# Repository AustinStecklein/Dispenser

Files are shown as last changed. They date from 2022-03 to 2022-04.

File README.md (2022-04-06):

# Dispenser
Creedmoor code base for the powder dispenser

# TODO List Software
- [ ] forward and back buttons dont function
- [ ] brightness/sound page sliders need to be prettier if possible
- [ ] calibrate, default settings, power off need yes and no image buttons
- [ ] Force the Subpages of Settings to not appear after clicking on the home button   and then clicking on Settings
- [ ] Keyboard does the same thing as the Settings subpages
- [ ] Replace the Boot Logo when the Program starts with a Creedmoor Logo

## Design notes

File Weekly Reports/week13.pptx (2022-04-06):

## Gantt Chart

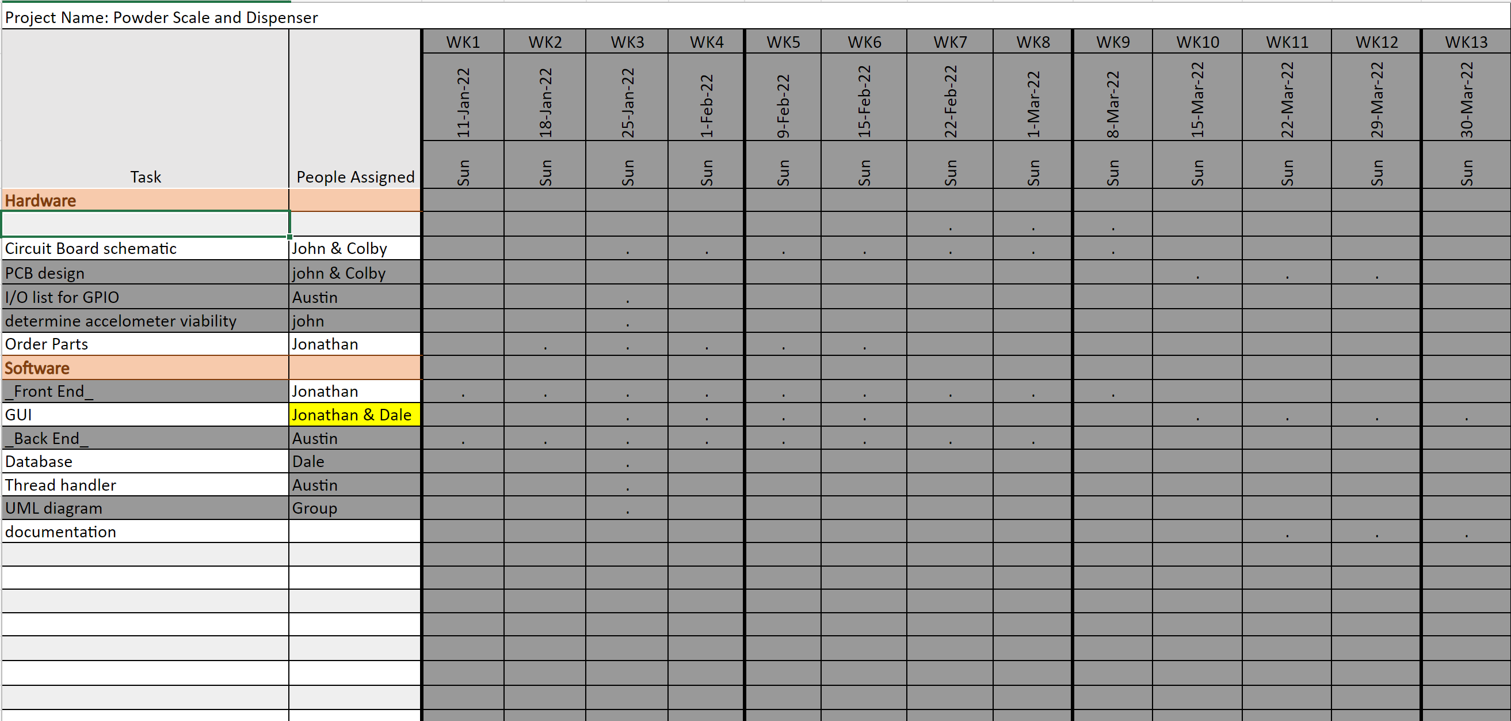
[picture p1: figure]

## Week 13 (30-Mar to 5-Apr) Austin

Goal/Task | % Done | Hours (Act.)

Hours on task during the week (On track ≥ 13 / wk)
Total hours on task so far this semester (On track ≥ 163 hrs)

## Progress made during the week (Log) (What I did)

For example: Resources found (links, manuals), Designs created, Decisions made and corresponding rational, Photos of prototype progress, etc.

## Difficulties encountered during the week (What I did not do and why)

## Goals for this coming week (Ones that move the project forward the most)

Goal/Task | Stop Date (Est.) | Hours (Est.)

Estimated time needed to work on goals for this coming week (typ. 13 hrs)

## How can we help you achieve your goals?

## Week 13 (30-Mar to 5-Apr) Jonathan Phillips

Goal/Task | % Done | Hours (Act.)
Front end - Documentation | N/A | 13
Front end – Fixed <,> buttons | 100 | 2
Front end - Testing | N/A | 3
Presentation | 100 | 0.5

Hours on task during the week (On track ≥ 13 / wk) | 18.5
Total hours on task so far this semester (On track ≥ 163 hrs) | 153

## Progress made during the week (Log) (What I did)

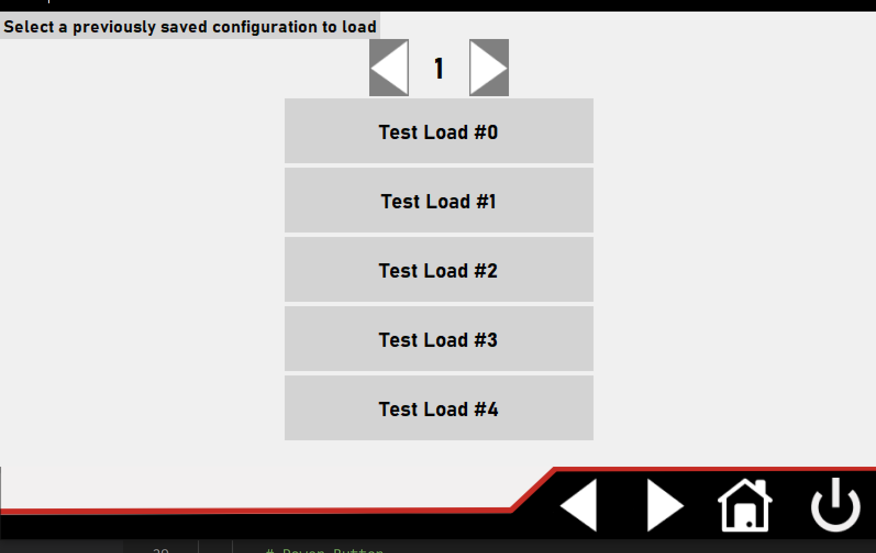
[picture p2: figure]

## Difficulties encountered during the week (What I did not do and why)

- Did not complete everything for Creedmoor due to time constraints

## Goals for this coming week (Ones that move the project forward the most)

Goal/Task | Stop Date (Est.) | Hours (Est.)
N/A | N/A | N/A

Estimated time needed to work on goals for this coming week (typ. 13 hrs) | N/A

## How can we help you achieve your goals?

## Week 13 (30-Mar to 5-Apr) Dale Andreoli

Goal/Task | % Done | Hours (Act.)
Finish comments and documentation | | 5
Final report – software part | | 3
Oral Presentation – create and present | | 4

Hours on task during the week (On track ≥ 13 / wk) | 12
Total hours on task so far this semester (On track ≥ 163 hrs) | 155

## Progress made during the week (Log) (What I did)

Finished comments and documentation
Created slides for presentation
Gave oral presentation with group
Wrote software part of final documentation report

## Difficulties encountered during the week (What I did not do and why)

- Not all backend features were able to be fully implemented such as some of the settings buttons and custom profile features

## Week 13 (30-Mar to 5-Apr) John Stinger

Goal/Task | % Done | Hours (Act.)

Hours on task during the week (On track ≥ 13 / wk)
Total hours on task so far this semester (On track ≥ 163 hrs)

## Progress made during the week (Log) (What I did)

For example: Resources found (links, manuals), Designs created, Decisions made and corresponding rational, Photos of prototype progress, etc.

## Difficulties encountered during the week (What I did not do and why)

## Goals for this coming week (Ones that move the project forward the most)

Goal/Task | Stop Date (Est.) | Hours (Est.)

Estimated time needed to work on goals for this coming week (typ. 13 hrs)

## How can we help you achieve your goals?

## Week 13 (30-Mar to 5-Apr) Colby Hatton

Goal/Task | % Done | Hours (Act.)
Documentation | 100 | 13

Hours on task during the week (On track ≥ 13 / wk)
Total hours on task so far this semester (On track ≥ 163 hrs)

## Progress made during the week (Log) (What I did)

Documented every step of the hardware design for this semesters senior project.

## Difficulties encountered during the week (What I did not do and why)

- Slight confusion in what needs to be done, resulting in some rewriting of parts of the documentation.

## Goals for this coming week (Ones that move the project forward the most)

Goal/Task | Stop Date (Est.) | Hours (Est.)
Graduate! | 4/7 | <5 (Length of the 380 final)

Estimated time needed to work on goals for this coming week (typ. 13 hrs)

## How can we help you achieve your goals?

- Pizza Party?

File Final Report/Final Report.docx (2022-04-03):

Powder Scale and Dispenser

Team A: Dale Andreoli, Colby Hatton, Jonathan Phillips, Austin Stecklein, John Stinger

Index

1. Mission Statement
2. Scope of Work
3. Design Specifications
    i. Stuff
    ii. Things
4. Product Selection
5. Body
  a. Hardware
  b. Software
6. Conclusion

Mission Statement

Design, build, and test the electronics for the dispenser with a touch screen display and controlling two stepper motors by April 6, 2021 with a prototyping budget of $1,000.00 USD and for less than 600 people-hours.

Scope of Work

Design Specifications

Product Selection

- We chose the beaglebone back because that was the board that Creedmoor provided for us and concluded that after the prototype was handed back to Creedmoor they would be able to move the project along faster versus using a different board. We also choose to use the GeeekPi screen due to the high volumes of stock available at Digikey, and other website, when it came time for Creedmoor to mass produce.

Body

User’s Manual

- The primary function of the prototype is to dispense powder according to a user inputted value which then displays the current value on the scale to the prototype’s user interface.
- The prototype consists of beaglebone black wireless development board, with a powder scale connected to it via an USB connection, as well as an user interface displayed on a 5 inch screen, which is the way by which the user interacts with the prototype.

Developer’s Report

Software

- The programming language used to create the front and back end of the user interface was Python. We chose Python because it is a relatively easy language to learn, read, and understand.
- As previously mentioned, the software is broken up into 2 major sections: the front end and the back end. The front end is then broken up into different pages, each with their own purpose and function. The home page is the first screen users will see after booting up the prototype. However, the home page, and every other page, is slightly covered by another page known as main. Main consists of a black bar with 4 buttons, which allow the user to navigate directly back to the home page and turn off the prototype. The settings page is a hub for the different types of settings an user could interact with, for example, the brightness and sound of the prototype. When the user wants to create a new profile, or Load Card, they can click on the Save button on the home page and are directed to a page containing a filename along with several other fields that are involved with reloading ammunition. The user can save their own values and make notes onto a Load Card, and store that information for future use, which allows them to switch between Load Card depending on their current needs.
- The back end…
- The front end is designed to run on every machine, however, the back end is designed to run on a beaglebone black board with the powder scale feeding the beaglebone information via an USB connection.

Conclusion

The dispenser

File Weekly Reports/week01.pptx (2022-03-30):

## Creedmoor Powder Dispenser

## Weekly progress (Hardware)

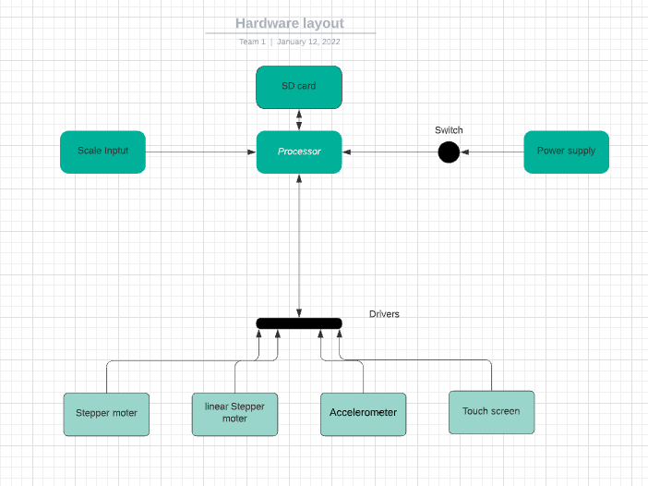
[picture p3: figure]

## Weekly progress (software)

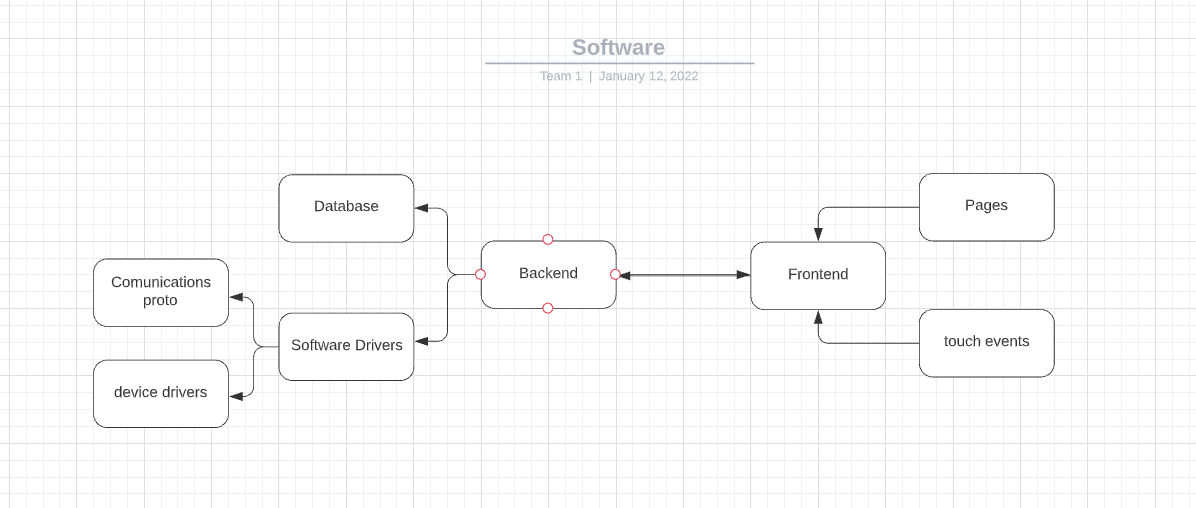
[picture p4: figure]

## Week 1 (5-Jan to 11-Jan) Austin Stecklein

Goal/Task | % Done | Hours (Act.)
Everyone Complete Leadership Foundation: Clarify Purpose (p. 32-33), Team Purpose Statement (p. 34), Voice Finder (p. 64-67), Your Contribution Statement (p. 68), Win-Win Performance Agreement (p. 76) | 0 | 0
Team Complete: Project Objective / Mission Statement (clear and concise, <25 words, see example below) | 100 | .5
Team Complete: Project Task Template (A Gantt Chart) (Conditions or tasks that must be completed, work that needs to be done) | 0 | 0
Flow charts for hardware and software | 100 | 5.5

Example Project Objective / Mission Statements
Power Scale Dispenser:
Design, build, and test the electronics for the dispenser with a touch screen display and controlling two stepper motors by April 6, 2021 with a prototyping budget of $XXX USD and for less than 600 people-hours.
For ideas, also read Mission Questions in I-Learn | Content | Resources | Mission Questions

Hours on task during the week (On track ≥ 13 / wk) | 6
Total hours on task so far this semester (On track ≥ 13 hrs) | 13

## Progress made during the week (Log) (What I did)

- Created general software and hardware layout
- Researched hardware parts

## Difficulties encountered during the week (What I did not do and why)

- Defining scope of project

## Goals for this coming week (Ones that move the project forward the most)

Goal/Task | Stop Date (Est.) | Hours (Est.)
Selecting processor for project with rest of the group. | 1/14/21 | 1
Researching drivers for stepper motors | 1/16/21 | 2
developing backend framework with chosen programming language | 1/26/21 | 10

Estimated time needed to work on goals for this coming week (typ. 13 hrs) | 13

## How can we help you achieve your goals?

- Understanding more of the final product

## Week 1 (5-Jan to 11-Jan) Jonathan Phillips

Goal/Task | % Done | Hours (Act.)
Everyone Complete Leadership Foundation: Clarify Purpose (p. 32-33), Team Purpose Statement (p. 34), Voice Finder (p. 64-67), Your Contribution Statement (p. 68), Win-Win Performance Agreement (p. 76)
Team Complete: Project Objective / Mission Statement (clear and concise, <25 words, see example below)
Team Complete: Project Task Template (A Gantt Chart) (Conditions or tasks that must be completed, work that needs to be done)

Power Scale Dispenser:
Design, build, and test the electronics for the dispenser with a touch screen display and controlling two stepper motors by April 6, 2021 with a prototyping budget of $XXX USD and for less than 600 people-hours.

Hours on task during the week (On track ≥ 13 / wk)
Total hours on task so far this semester (On track ≥ 13 hrs)

## Progress made during the week (Log) (What I did)

- Created a Gannt Chart for the layout for the hardware and software
- Researched different LCDs that could be used for the touch screen display

## Difficulties encountered during the week (What I did not do and why)

- Did not order the LCD screen yet due to it needing to be approved first by the group

## Goals for this coming week (Ones that move the project forward the most)

Goal/Task | Stop Date (Est.) | Hours (Est.)
Finalize parts for the project and order them | 1/13/22 | 1
Start Development on the Front End framework | 1/26/22 | 12

Estimated time needed to work on goals for this coming week (typ. 13 hrs) | 13

## How can we help you achieve your goals?

- Do you have a preference on what the screen will be?

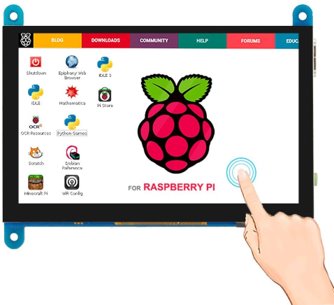
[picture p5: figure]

Elecrow

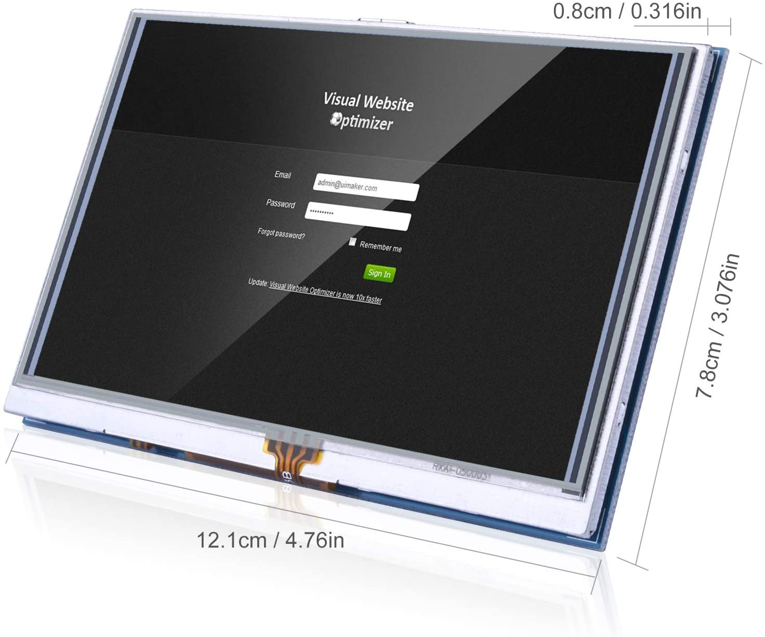
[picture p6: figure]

Kuman

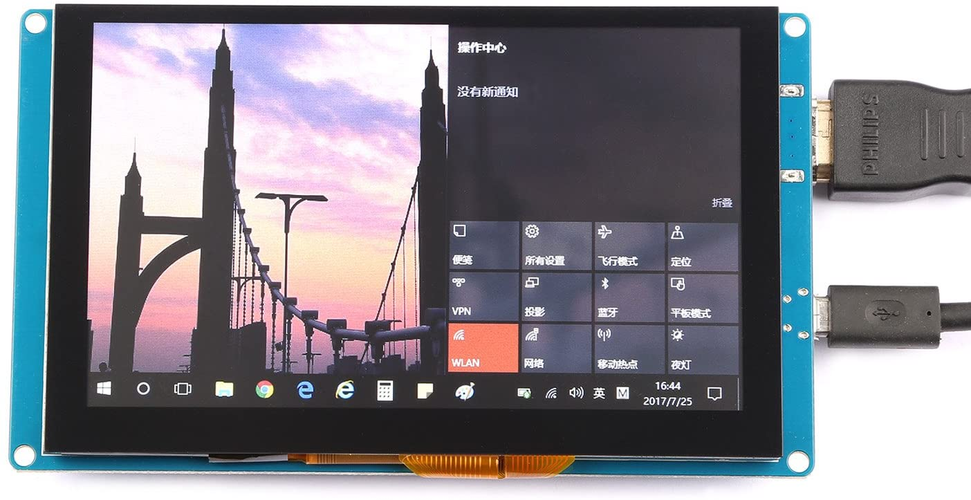
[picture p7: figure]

GeeekPi

## Week 1 (5-Jan to 11-Jan) Dale Andreoli

Goal/Task | % Done | Hours (Act.)
Everyone Complete Leadership Foundation: Clarify Purpose (p. 32-33), Team Purpose Statement (p. 34), Voice Finder (p. 64-67), Your Contribution Statement (p. 68), Win-Win Performance Agreement (p. 76) | 0 | 0
Team Complete: Project Objective / Mission Statement (clear and concise, <25 words, see example below) | 100 | 1
Team Complete: Project Task Template (A Gantt Chart) (Conditions or tasks that must be completed, work that needs to be done) | 35 | 1

Example Project Objective / Mission Statements
Power Scale Dispenser:
Design, build, and test the electronics for the dispenser with a touch screen display and controlling two stepper motors by April 6, 2021 with a prototyping budget of $XXX USD and for less than 600 people-hours.
For ideas, also read Mission Questions in I-Learn | Content | Resources | Mission Questions

Hours on task during the week (On track ≥ 13 / wk) | 5
Total hours on task so far this semester (On track ≥ 13 hrs) | 5

## Progress made during the week (Log) (What I did)

- Researched potential processors

## Difficulties encountered during the week (What I did not do and why)

- Determining what we need to do and how to divide it

## Goals for this coming week (Ones that move the project forward the most)

Goal/Task | Stop Date (Est.) | Hours (Est.)
Research potential processors | 1/14/21 | 2
Collaborate as a group to determine which processors would be best | 1/16/21 | 4
Research methods to implement necessary drivers | 1/26/21 | 6

Estimated time needed to work on goals for this coming week (typ. 13 hrs) | 12

## How can we help you achieve your goals?

- Clarify/Answer Questions

## Week 1 (5-Jan to 11-Jan) Colby Hatton

Goal/Task | % Done | Hours (Act.)
Everyone Complete Leadership Foundation: Clarify Purpose (p. 32-33), Team Purpose Statement (p. 34), Voice Finder (p. 64-67), Your Contribution Statement (p. 68), Win-Win Performance Agreement (p. 76)
Team Complete: Project Objective / Mission Statement (clear and concise, <25 words, see example below)
Team Complete: Project Task Template (A Gantt Chart) (Conditions or tasks that must be completed, work that needs to be done)

Project Objective / Mission Statements
Power Scale Dispenser:
Design, build, and test the electronics for the dispenser with a touch screen display and controlling two stepper motors by April 6, 2021 with a prototyping budget of $XXX USD and for less than 600 people-hours.
For ideas, also read Mission Questions in I-Learn | Content | Resources | Mission Questions

Hours on task during the week (On track ≥ 13 / wk) | ~5
Total hours on task so far this semester (On track ≥ 13 hrs) | ~5

## Progress made during the week (Log) (What I did)

- Helped create general software and hardware layout
- Purchased leadership book
- Preliminary research

## Difficulties encountered during the week (What I did not do and why)

- No problems yet

## Goals for this coming week (Ones that move the project forward the most)

Goal/Task | Stop Date (Est.) | Hours (Est.)
Find, compare, and form opinions on the correct processor for our project. | 1/14/22 | 4
Selecting processor for project with rest of the group. | 1/16/22 | 1
Obtain, test, and experiment with given hardware | 1/16/22 | 3
Class time, presentations, workbook, etc. | 1/16/22 | 4

Estimated time needed to work on goals for this coming week (typ. 13 hrs) | 13

## How can we help you achieve your goals?

- Communication - Ensure lines work and communication is clear.

## Week 1 (5-Jan to 11-Jan) John Stinger

Goal/Task | % Done | Hours (Act.)
Everyone Complete Leadership Foundation: Clarify Purpose (p. 32-33), Team Purpose Statement (p. 34), Voice Finder (p. 64-67), Your Contribution Statement (p. 68), Win-Win Performance Agreement (p. 76)
Team Complete: Project Objective / Mission Statement (clear and concise, <25 words, see example below)
Team Complete: Project Task Template (A Gantt Chart) (Conditions or tasks that must be completed, work that needs to be done)

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

Hours on task during the week (On track ≥ 13 / wk) | 12
Total hours on task so far this semester (On track ≥ 13 hrs) | 12

## Progress made during the week (Log) (What I did)

Researched different processors and possible boards to use in the project.

Atmel ARM based microprocessor would be best.

Raspberry Pi Zero 2 would be effective and affordable, but generally unavailable.

Do we want a commercially available board?

## Difficulties encountered during the week (What I did not do and why)

- Select a specific processor. Needed to meet with the team to discuss options.

## Goals for this coming week (Ones that move the project forward the most)

Goal/Task | Stop Date (Est.) | Hours (Est.)
Select a Processor | | 1
Define the exact scope of the project | | 2
Define individual roles | | 1
Purchasing a Board | | 2

Estimated time needed to work on goals for this coming week (typ. 13 hrs)

## How can we help you achieve your goals?

- More than one day to do research and meet with the team.

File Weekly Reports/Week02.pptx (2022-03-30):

## Week 2 (13-Jan to 18-Jan)

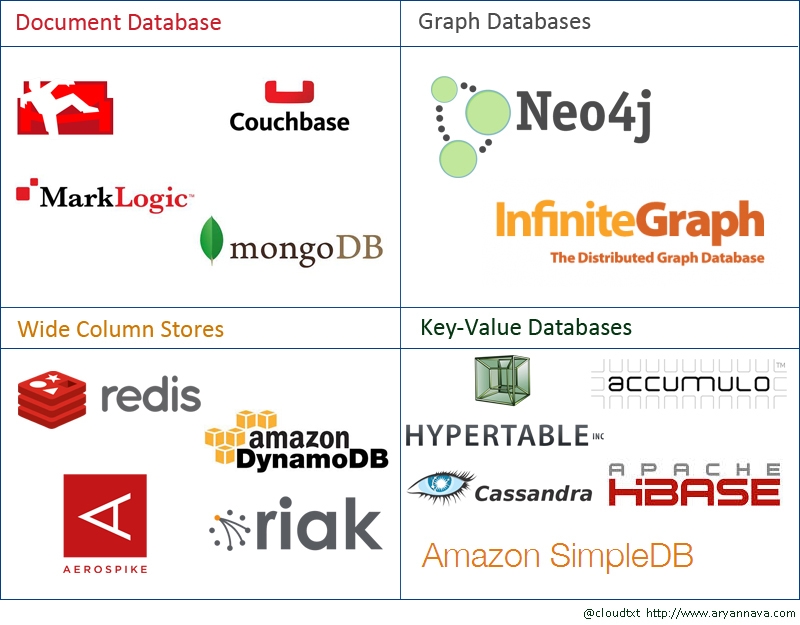
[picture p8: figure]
NoSQL vs SQL | What is Difference between SQL and NoSQL |
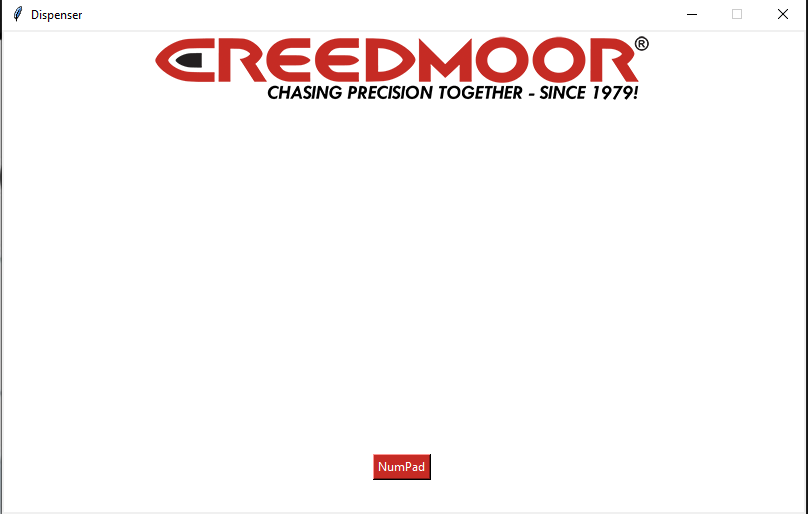
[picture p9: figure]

## Week 2 (13-Jan to 18-Jan) Austin Stecklein

Goal/Task | % Done | Hours (Act.)
Backend (event handling and threading) | 50 | 8
I/O list for circuit schematic | 100 | 1
Drivers for steppers and accleometer | 10 | 4

Hours on task during the week (On track ≥ (13) / wk) | 13
Total hours on task so far this semester (On track ≥ 26 hrs) | 26

## Progress made during the week (Log) (What I did)

Created event handler and successfully test running events from a pop GUI
Create I/O list for use in schematic
MicroSD card on order

## Difficulties encountered during the week (What I did not do and why)

- No SD card was found in package

## Goals for this coming week (Ones that move the project forward the most)

Goal/Task | Stop Date (Est.) | Hours (Est.)
Finish event handler by allowing data to pass from the thread back to the GUI | 1/26 | 6
Get Code onto the beagle board | 1/26 | 2
Get stepper motor driver working | 1/26 | 6

Estimated time needed to work on goals for this coming week (typ. 13 hrs) | 14

## How can we help you achieve your goals?

## Week 2 (12-Jan to 18-Jan) Dale Andreoli

Goal/Task | % Done | Hours (Act.)
Everyone Complete Leadership Foundation: Clarify Purpose (p. 32-33), Team Purpose Statement (p. 34), Voice Finder (p. 64-67), Your Contribution Statement (p. 68), Win-Win Performance Agreement (p. 76) | 0 | 0
Research database options – Amazon Dynamo DB | 100 | 3
Assist with GUI – Research tkinter Python library, create mockup | 10 | 1

Project Objective / Mission Statements
Power Scale Dispenser:
Design, build, and test the electronics for the dispenser with a touch screen display and controlling two stepper motors by April 6, 2021 with a prototyping budget of $XXX USD and for less than 600 people-hours.

Hours on task during the week | 4
Total hours on task so far this semester | 17

## Progress made during the week (Log) (What I did)

- Collaborated with Austin on our needs for backend software
- Researched NoSQL database options
  - Amazon Dynamo DB should fit our needs

## Difficulties encountered during the week (What I did not do and why)

- No problems yet

## Goals for this coming week (Ones that move the project forward the most)

Goal/Task | Stop Date (Est.) | Hours (Est.)
Work with Jonathon to design GUI | 1/23/21 | 3
Implement GUI features | 1/24/21 | 6
Collaborate with Austin to determine what drivers will need to be written | 1/23/21 | 2

Estimated time needed to work on goals for this coming week | 11

## How can we help you achieve your goals?

- GUI thoughts and ideas

## Week 2 (13-Jan to 18-Jan) John Stinger

Goal/Task | % Done | Hours (Act.)
Decide on a specific development board for the project. | 100% | 3
Meet with team to discus the scope and define roles | 100% | 2

Hours on task during the week (On track ≥ (13) / wk) | 10
Total hours on task so far this semester (On track ≥ 26 hrs) | 22

## Progress made during the week (Log) (What I did)

For example: Resources found (links, manuals), Designs created, Decisions made and corresponding rational, Photos of prototype progress, etc.

- Inspected the material received

- Decided to continue using the provided Beagle Board for development

- Defined the scope better and the individual roles and goals

## Difficulties encountered during the week (What I did not do and why)

- None

## Goals for this coming week (Ones that move the project forward the most)

Goal/Task | Stop Date (Est.) | Hours (Est.)
Check viability of current accelerometer | | 2
Start the drafting of the circuit board | | 10 +

Estimated time needed to work on goals for this coming week (typ. 13 hrs) | 12 +

## How can we help you achieve your goals?

- Continued direction

- Advice on circuit building software

- Did we want any kind of wireless capabilitie?

- Can the power supply be its own board?

## Week 2 (13-Jan to 18-Jan) Jonathan Phillips

Goal/Task | % Done | Hours (Act.)
Reviewed the Hardware sent from Creedmoor | 100 | 1.5
Ordered the LCD Screen (Arriving Today) | 100 | 0.5
Worked on the front end | TBD | 5

Hours on task during the week (On track ≥ (13) / wk)
Total hours on task so far this semester (On track ≥ 26 hrs)

## Progress made during the week (Log) (What I did)

For example: Resources found (links, manuals), Designs created, Decisions made and corresponding rational, Photos of prototype progress, etc.

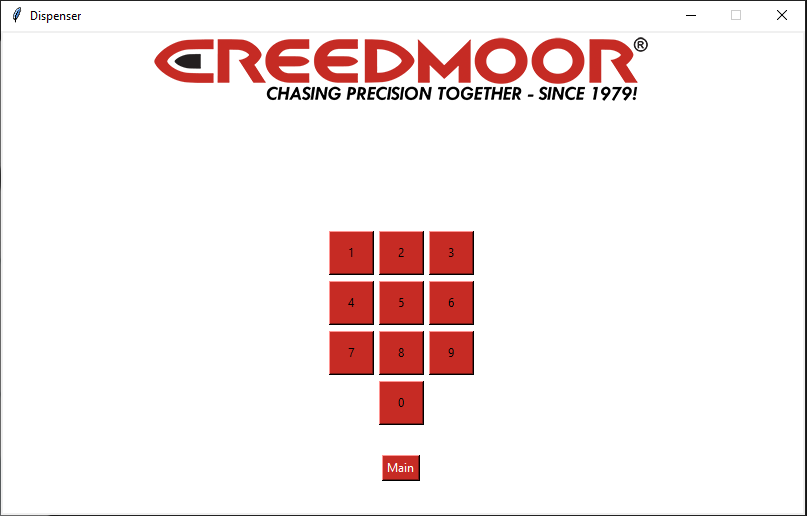
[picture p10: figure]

## Difficulties encountered during the week (What I did not do and why)

- Understanding Python

## Goals for this coming week (Ones that move the project forward the most)

Goal/Task | Stop Date (Est.) | Hours (Est.)
UML Diagram for the frontend | 1/25/22 | 1.5
Continue working on the frontend | Ongoing | 11.5

Estimated time needed to work on goals for this coming week (typ. 13 hrs) | 13

## How can we help you achieve your goals?

- Do you have an idea of what you would like the layout of the display to be?

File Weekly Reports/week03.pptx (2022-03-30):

## Week 3 (19-Jan to 25-Jan)

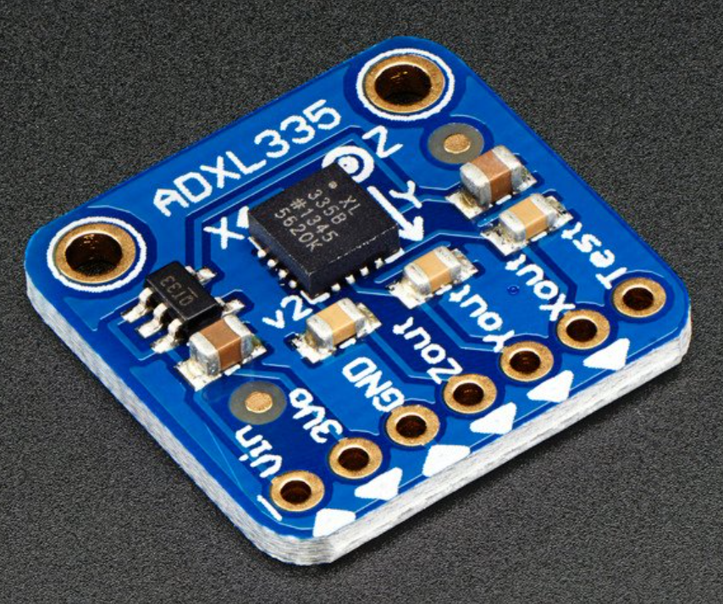
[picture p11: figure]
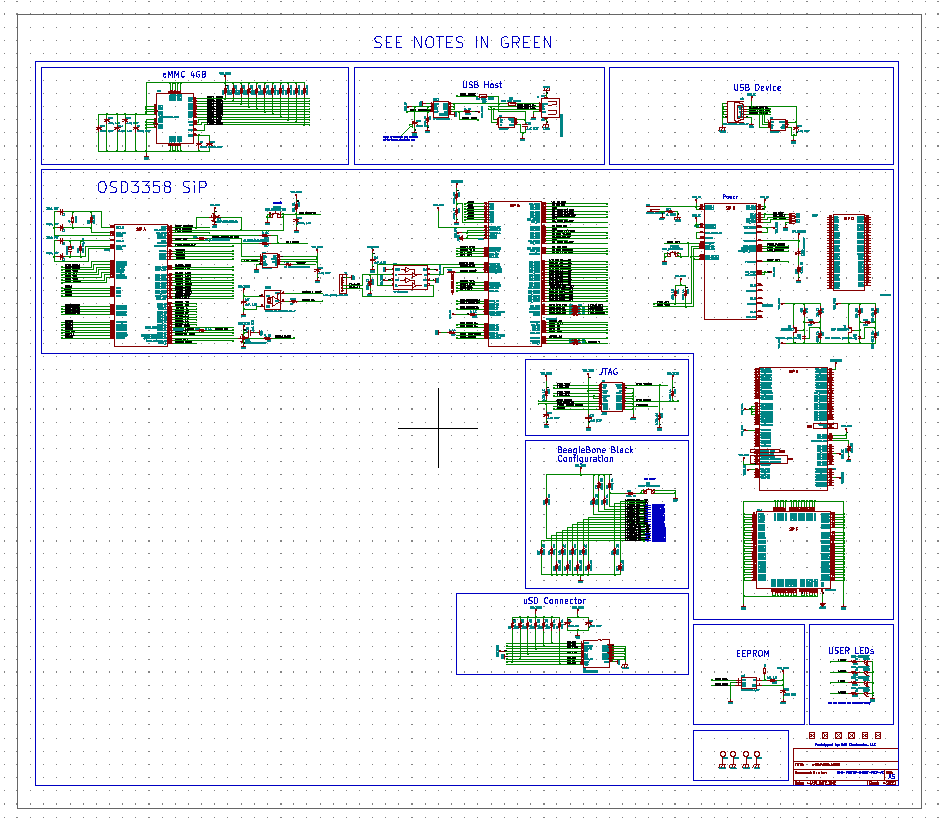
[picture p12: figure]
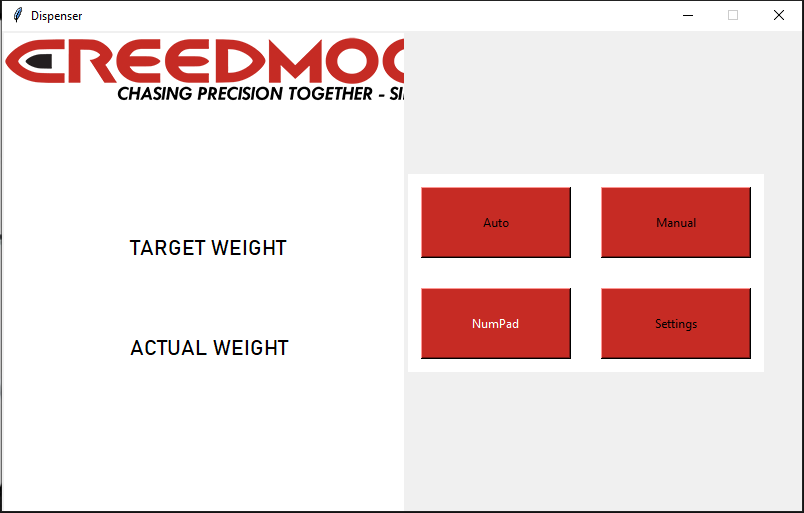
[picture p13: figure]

## Week 3 (19-Jan to 25-Jan) Austin Stecklein

Goal/Task | % Done | Hours (Act.)
Get stepper motor driver working | 80 | 6
Get Code onto the beagle board | 100 | 2
Finish event handler by allowing data to pass from the thread back to the GUI | 100 | 4

Hours on task during the week (On track ≥ (10) / wk) | 12
Total hours on task so far this semester (On track ≥ 36 hrs) | 30

## Progress made during the week (Log) (What I did)

Re-flashed memory on the Beaglebone black
Used PWM library to control the stepper motors more accurately
Uploaded code onto the Beaglebone black
Finished backend event framework

## Difficulties encountered during the week (What I did not do and why)

- Flashing the Board had some hiccups
- Understanding the usb capabilities

## Goals for this coming week (Ones that move the project forward the most)

Goal/Task | Stop Date (Est.) | Hours (Est.)
Finish stepper motor drivers | 2/2/2022 | 2
Get database framework | 2/2/2022 | 3
Start interfacing with prototype GUI | 2/2/2022 | 6

Estimated time needed to work on goals for this coming week (typ. 13 hrs) | 11

## Week 3 (19-Jan to 25-Jan) Colby Hatton

Goal/Task | % Done | Hours (Act.)
Determine Which CAD Software to Use | 90 | 3
Create Basic Schematic and Accustom self to CAD Software | 60 | 5
Find Component Symbols/Footprints | 40 | 5

Hours on task during the week (On track ≥ (10) / wk) | 13
Total hours on task so far this semester (On track ≥ 36 hrs) | ~35

## Progress made during the week (Log) (What I did)

Determined that we will be using KiCad to design and lay out our project.
Found Footprint and Symbol Libraries for several components we will be using.
Successfully found and Imported the Beagle Board Black Wireless board and Schematic

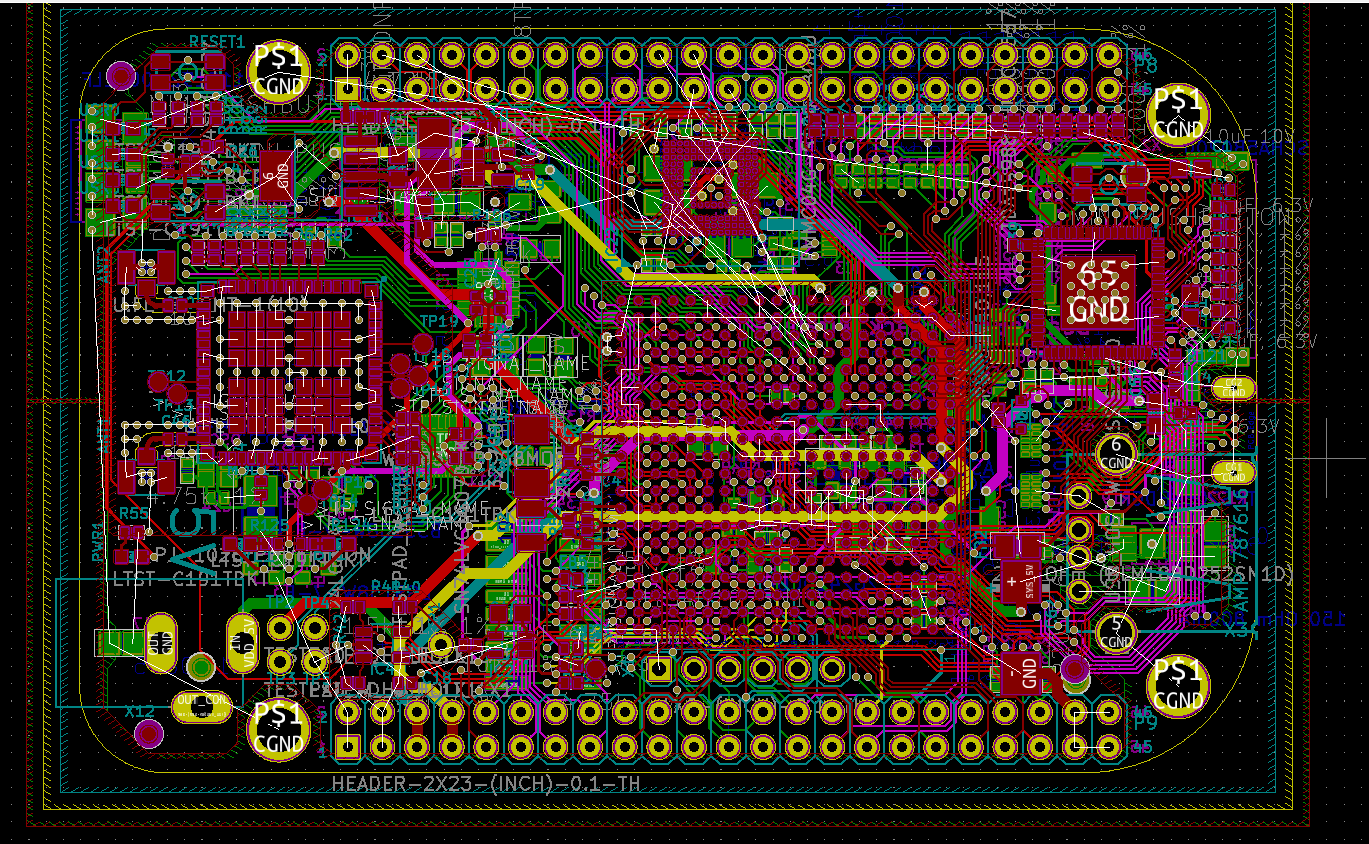
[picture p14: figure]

## Difficulties encountered during the week (What I did not do and why)

- Certain components out of production
- Need to find alternate and ensure they are compatible with the same pinout

## Goals for this coming week (Ones that move the project forward the most)

Goal/Task | Stop Date (Est.) | Hours (Est.)
Acquire footprints/symbols for the components we will be using | 2/9 | 6
Finish/Wire schematic for our PCB | 2/16 | 20
(Possibly) Plan layout of the board | 2/16 | 5

Estimated time needed to work on goals for this coming week (typ. 13 hrs) | ~15

## Week 3 (19-Jan to 25-Jan) Dale Andreoli

Goal/Task | % Done | Hours (Act.)
Assist with GUI design/mockup | 90 | 3
GUI – Number pad module | 85 | 8

Project Objective / Mission Statements
Power Scale Dispenser:
Design, build, and test the electronics for the dispenser with a touch screen display and controlling two stepper motors by April 6, 2021 with a prototyping budget of $XXX USD and for less than 600 people-hours.

Hours on task during the week | 11
Total hours on task so far this semester | 30

## Progress made during the week (Log) (What I did)

Collaborated with Jonathon on the GUI
Created a Number Pad module that can be easily added into the GUI

## Goals for this coming week (Ones that move the project forward the most)

Goal/Task | Stop Date (Est.) | Hours (Est.)
Next GUI module: Pop out menu | 2/1/21 | 8
Collaborate with Jonathan for GUI needs | 2/1/21 | 3

Estimated time needed to work on goals for this coming week | 11

## How can we help you achieve your goals?

- Jonathan and I will reach out to Christian, Kelby and Wayne for GUI feedback.

## Week 3 (19-Jan to 25-Jan) John Stinger

Goal/Task | % Done | Hours (Act.)
Check viability of current accelerometer | 100% | 2
Start the drafting of the circuit board | 100% | 4

Hours on task during the week (On track ≥ (10) / wk) | 6
Total hours on task so far this semester (On track ≥ 36 hrs)

## Progress made during the week (Log) (What I did)

For example: Resources found (links, manuals), Designs created, Decisions made and corresponding rational, Photos of prototype progress, etc.

- 3 axis will be fine
- Both the premade card and buying the chip would be viable
- Started the modeling with Colby on KiCad

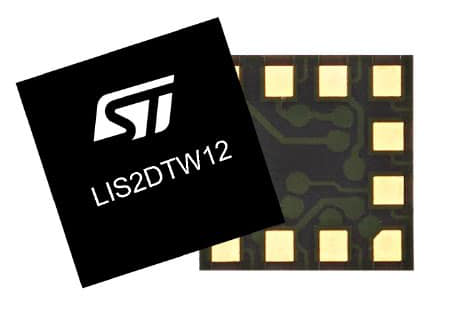
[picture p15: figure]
LIS2DTW12TR

## Difficulties encountered during the week (What I did not do and why)

- none

## Goals for this coming week (Ones that move the project forward the most)

Goal/Task | Stop Date (Est.) | Hours (Est.)
Continue to model the circuit card on the computer. | | 10+
Learn how to make the motor drivers more robust. | | 3

Estimated time needed to work on goals for this coming week (typ. 13 hrs)

## How can we help you achieve your goals?

- Continue to be available for reference.

## Week 3 (19-Jan to 25-Jan) Jonathan Phillips

Goal/Task | % Done | Hours (Act.)
UML Mockup | 100 | 1
Front End | N/A | 6.5

Hours on task during the week (On track ≥ (10) / wk) | 8.5
Total hours on task so far this semester (On track ≥ 36 hrs)

## Progress made during the week (Log) (What I did)

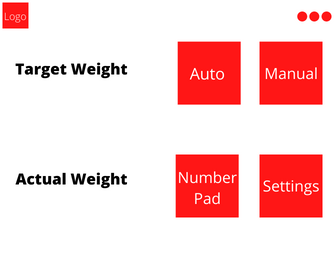
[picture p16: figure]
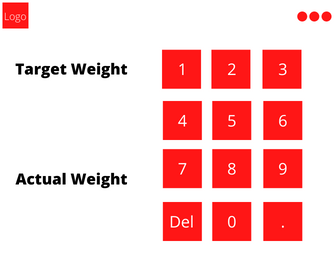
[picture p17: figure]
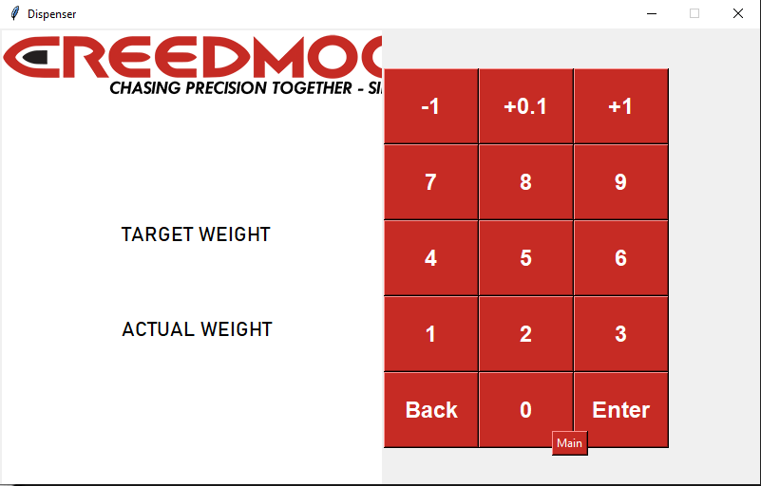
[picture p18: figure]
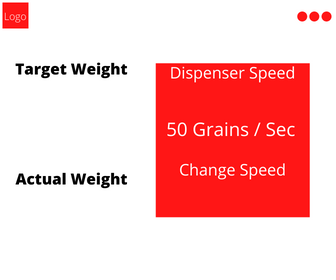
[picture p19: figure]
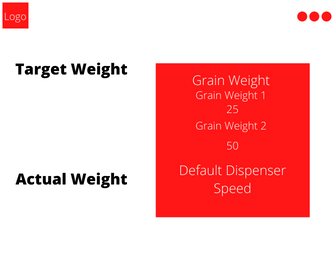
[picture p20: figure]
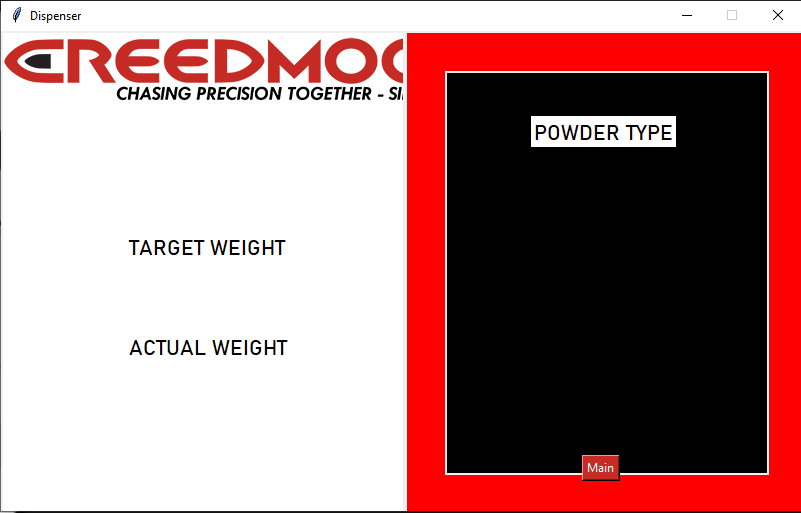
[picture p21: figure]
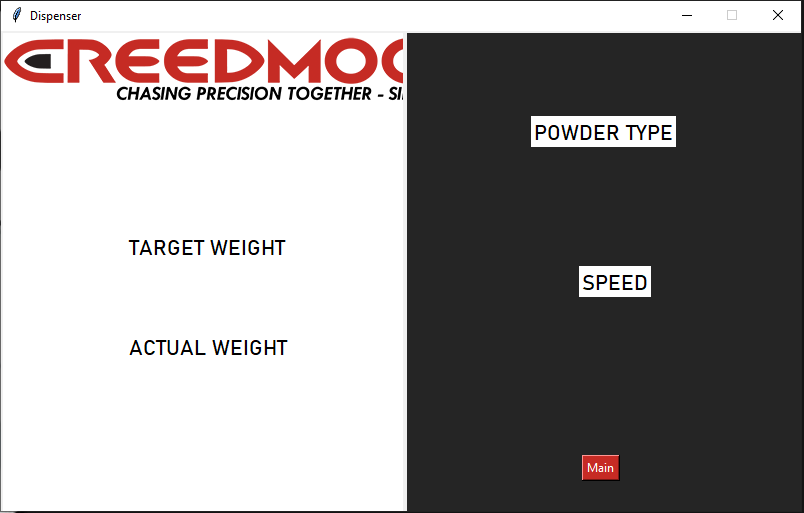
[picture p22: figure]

Front end

UML Mockup

## Difficulties encountered during the week (What I did not do and why)

- Learning Python syntax

## Goals for this coming week (Ones that move the project forward the most)

Goal/Task | Stop Date (Est.) | Hours (Est.)
Front end | Ongoing | 13

Estimated time needed to work on goals for this coming week (typ. 13 hrs) | 13

## How can we help you achieve your goals?

- Any comments on the mockup or overall design of the front end?

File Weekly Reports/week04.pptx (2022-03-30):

## Week 4 (26-Jan to 1-Feb) Austin Stecklein

Goal/Task | % Done | Hours (Act.)
Finish stepper motor drivers | 100 | 4
Get database framework | 50 | 3
Investigate hardware | 50 | 6

Hours on task during the week (On track ≥ 13 / wk) | 13
Total hours on task so far this semester (On track ≥ 49 hrs) | 43

## Progress made during the week (Log) (What I did)

Software stepper drivers are complete
Database framework is moving along
Ordered another beagle bone to replace broken hardware

## Difficulties encountered during the week (What I did not do and why)

- Blowing up the hardware

## Goals for this coming week (Ones that move the project forward the most)

Goal/Task | Stop Date (Est.) | Hours (Est.)
Finish investigating hardware | 2/10/2021 | 4
Finish database | 2/10/2021 | 4
Help with GUI | 2/10/2021 | 6

Estimated time needed to work on goals for this coming week (typ. 13 hrs) | 14

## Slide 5

Week 4 (26-Jan to 1-Feb) Colby Hatton

Goal/Task | % Done | Hours (Act.)
Finish Schematic | 70 | 6
Finish PCB | 5 | 1
Part/Research

Hours on task during the week (On track ≥ 13 / wk)
Total hours on task so far this semester (On track ≥ 49 hrs)

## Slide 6

Progress made during the week (Log)
(What I did)

Found and applied parts to Schematic (Mostly connectors)
Researched Memory Module
Attempted to fix BeagleBoard

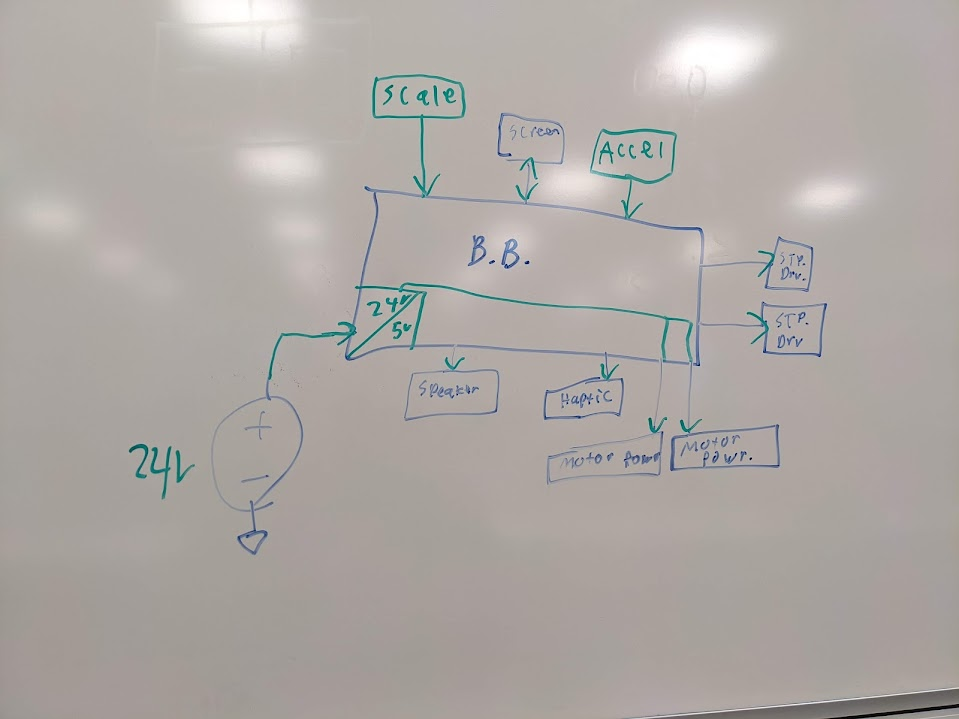
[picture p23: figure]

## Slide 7

Difficulties encountered during the week
(What I did not do and why)

- Assign lines to pins
- Physical Work with the BeagleBoard

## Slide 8

Goals for this coming week
(Ones that move the project forward the most)

Goal/Task | Stop Date (Est.) | Hours (Est.)
Finish Schematic | | 4
Begin Layout | | 8

Estimated time needed to work on goals for this coming week (typ. 13 hrs)

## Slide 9

How can we help you achieve your goals?

- Part Acquisition
- Line Assignments

## Week 4 (26-Jan to 2-Feb) Dale Andreoli

Goal/Task | % Done | Hours (Act.)
Collaborate with team on UI design and implementation | 100 | 2
Research open source projects to save time creating GUI modules from scratch | 50 | 3
Research other potential libraries to use instead of tkinter | 50 | 1
Implement GUI modules | 15 | 6

Project Objective / Mission Statements
Power Scale Dispenser:
Design, build, and test the electronics for the dispenser with a touch screen display and controlling two stepper motors by April 6, 2021 with a prototyping budget of $1000 USD and for less than 600 people-hours.

Hours on task during the week | 12
Total hours on task so far this semester | 42

## Progress made during the week (Log) (What I did)

Collaborated with team on UI design and implementation
Researched libraries and projects to save time creating GUI modules from scratch
Researched other potential libraries to use instead of tkinter

## Difficulties encountered during the week (What I did not do and why)

- We now have a nice clear plan for what the UI needs

## Goals for this coming week (Ones that move the project forward the most)

Goal/Task | Stop Date (Est.) | Hours (Est.)
Find or design a touch keyboard module to be used in the GUI | Feb 9th | 9
Collaborate with Jonathan and Austin on GUI implementation | | 3

Estimated time needed to work on goals for this coming week | 12

## Week 4 (26-Jan to 1-Feb) John Stinger

Goal/Task | % Done | Hours (Act.)
Board Design | 15% | 4
Component Selection | 70% | 4
Team Meetings and Discussions | | 3

Hours on task during the week (On track ≥ 13 / wk) | 11
Total hours on task so far this semester (On track ≥ 49 hrs) | 39

## Progress made during the week (Log) (What I did)

For example: Resources found (links, manuals), Designs created, Decisions made and corresponding rational, Photos of prototype progress, etc.

- Continued the board design process
- Selected components for the I/O connections
- Ordered the components

## Difficulties encountered during the week (What I did not do and why)

- Certain components were unorderable

## Goals for this coming week (Ones that move the project forward the most)

Goal/Task | Stop Date (Est.) | Hours (Est.)
Continue to work on the board schematic | | 6
Continue to work on the board layout | | 6

Estimated time needed to work on goals for this coming week (typ. 13 hrs) | 12

## How can we help you achieve your goals?

- Is the motor drivers going to be integrated into the main board?

## Week 4 (26-Jan to 1-Feb) Jonathan Phillips

Goal/Task | % Done | Hours (Act.)
Front End | N/A | 11

Hours on task during the week (On track ≥ 13 / wk) | 11
Total hours on task so far this semester (On track ≥ 49 hrs) | 40

## Progress made during the week (Log) (What I did)

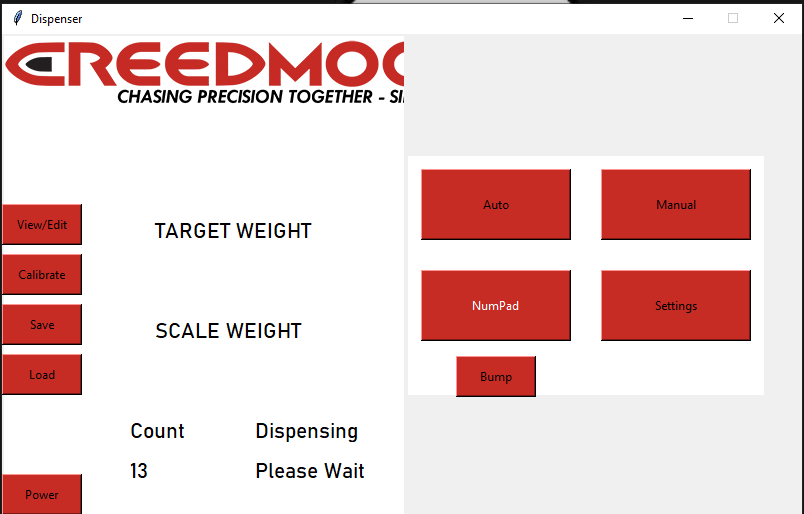
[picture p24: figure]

## Difficulties encountered during the week (What I did not do and why)

- The buttons cannot be modified that much using this python library,
However, the buttons can be made using images instead

## Goals for this coming week (Ones that move the project forward the most)

Goal/Task | Stop Date (Est.) | Hours (Est.)
Front End | 4/1/22 | 13

Estimated time needed to work on goals for this coming week (typ. 13 hrs) | 13

## How can we help you achieve your goals?

- Refining UI Design and Layout

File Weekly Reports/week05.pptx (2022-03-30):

## Week 5 (2-Feb to 8-Feb)


## Week 5 (2-Feb to 8-Feb) Austin Stecklein

Goal/Task | % Done | Hours (Act.)
Investigating hardware | 100 | 3
Finish database | 99 | 4
Backend events | 75 | 6

Hours on task during the week (On track ≥ 13 / wk) | 13
Total hours on task so far this semester (On track ≥ 62 hrs) | 56

## Progress made during the week (Log) (What I did)

Found that voltage regular to be the problem. Will take these lessons learned for future hardware
Finish database and interface for the GUI.
Continued to work on the PID and physical events.

## Difficulties encountered during the week (What I did not do and why)

- None

## Goals for this coming week (Ones that move the project forward the most)

Goal/Task | Stop Date (Est.) | Hours (Est.)
Finish backend events and start testing them with replacement beagle bone (lower voltage this time) | 2/16/2021 | 6
Finish PID and start experimenting with finding the best coefficients | 2/16/2021 | 5
Start merging GUI and backend | 2/16/2021 | 4

Estimated time needed to work on goals for this coming week (typ. 13 hrs) | 15

## Week 5 (2-Feb to 8-Feb) John Stinger

Goal/Task | % Done | Hours (Act.)
Continue to work on the board schematic | | 4
Continue to work on the board layout | | 4
Other | | 4

Hours on task during the week (On track ≥ 13 / wk) | 12
Total hours on task so far this semester (On track ≥ 62 hrs) | 51

## Progress made during the week (Log) (What I did)

- Board development
- Found different connectors
- Started testing speakers

## Difficulties encountered during the week (What I did not do and why)

- none

## Goals for this coming week (Ones that move the project forward the most)

Goal/Task | Stop Date (Est.) | Hours (Est.)
Continued Development of the board | Ongoing | 7
Research how to design better board drivers | | 3

Estimated time needed to work on goals for this coming week (typ. 13 hrs) | 12

## How can we help you achieve your goals?

- Continued Support

## Week 5 (2-Feb to 8-Feb) Colby Hatton

Goal/Task | % Done | Hours (Act.)
Schematic Work | 85% | 10
Layout | 5% | 1
Parts/Resarch/Testing | 80% | 2

Hours on task during the week (On track ≥ 13 / wk)
Total hours on task so far this semester (On track ≥ 62 hrs) | 51

## Progress made during the week (Log) (What I did)

Preformed MicroSD boot, verified speaker arrangement, prepared pin layout

## Difficulties encountered during the week (What I did not do and why)

- Finding a good motor driver

## Goals for this coming week (Ones that move the project forward the most)

Goal/Task | Stop Date (Est.) | Hours (Est.)
Obtain Motor Driver | Ongoing | 13
Finish Schematic
Contuine Layout

Estimated time needed to work on goals for this coming week (typ. 13 hrs) | 13

## How can we help you achieve your goals?

- Continued Support, consistently updated line/signal list

## Week 5 (3-Feb to 9-Feb) Dale Andreoli

Goal/Task | % Done | Hours (Act.)
Find or create a touch keyboard module to slot into the GUI | 80% | 5
Collaborate with Jonathan and Austin on GUI implementation | | 9

Project Objective / Mission Statements
Power Scale Dispenser:
Design, build, and test the electronics for the dispenser with a touch screen display and controlling two stepper motors by April 6, 2021 with a prototyping budget of $1000 USD and for less than 600 people-hours.

Hours on task during the week | 14
Total hours on task so far this semester | 56

## Progress made during the week (Log) (What I did)

Found a keyboard that should suit our needs after some modification
Refactored some of the GUI code to better apply principles of abstraction
Collaborated with Jonathan and Austin on GUI implementation


## Difficulties encountered during the week (What I did not do and why)

- Jonathan and I were getting some errors from the library as we tried to put the GUI code into different files

## Goals for this coming week (Ones that move the project forward the most)

Goal/Task | Stop Date (Est.) | Hours (Est.)
Finish implementing the keyboard | | 3
Collaborate with Jonathan and Austin on what GUI pages to implement next | | 9

Estimated time needed to work on goals for this coming week | 12

## Week 5 (2-Feb to 8-Feb) Jonathan Phillips

Goal/Task | % Done | Hours (Act.)
Front End | Ongoing | 11

Hours on task during the week (On track ≥ 13 / wk) | 11
Total hours on task so far this semester (On track ≥ 62 hrs) | 51

## Progress made during the week (Log) (What I did)


## Difficulties encountered during the week (What I did not do and why)

Python doesn’t like circular imports

## Goals for this coming week (Ones that move the project forward the most)

Goal/Task | Stop Date (Est.) | Hours (Est.)
Front End | Ongoing | 13

Estimated time needed to work on goals for this coming week (typ. 13 hrs) | 13

## How can we help you achieve your goals?

- Continued Support

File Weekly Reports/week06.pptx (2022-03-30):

## Week 6 (9-Feb to 15-Feb)


## Week 6 (9-Feb to 15-Feb) Austin Stecklein

Goal/Task | % Done | Hours (Act.)
Finish backend events and start testing them with replacement beagle bone | 50 | 6
Finish PID and start experimenting with finding the best coefficients | 25 | 3
Start merging GUI and backend | 50 | 3
Coordinating GUI and hardware direction | NA | 2

Hours on task during the week (On track ≥ 13 / wk) | 14
Total hours on task so far this semester (On track ≥ 75 hrs) | 70

## Progress made during the week (Log) (What I did)

Started merging backend and frontend
Testing backend on the beaglebone
Determining realistic deliverable with time frame

## Difficulties encountered during the week (What I did not do and why)

- GUI change

## Goals for this coming week (Ones that move the project forward the most)

Goal/Task | Stop Date (Est.) | Hours (Est.)
Finish merging frontend and backend | 2/23 | 6
Get prototype working | 2/23 | 6
start documentation | 2/23 | 10

Estimated time needed to work on goals for this coming week (typ. 13 hrs) | 13

## Week 6 (9-Feb to 15-Feb) Colby Hatton

Goal/Task | % Done | Hours (Act.)
Schematic | 90% | 4
Layout | 10% | 5
Parts/Research/Testing | 80% | 2

Hours on task during the week (On track ≥ 13 / wk) | 13
Total hours on task so far this semester (On track ≥ 75 hrs) | ~75

## Progress made during the week (Log) (What I did)

Began board layout, imported components, defined board shape, took measurements for positioning, and cried at the rats nest that will have to be resolved.


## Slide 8


## Difficulties encountered during the week (What I did not do and why)

- Motor driver (See Johns Presentation)

## Goals for this coming week (Ones that move the project forward the most)

Goal/Task | Stop Date (Est.) | Hours (Est.)
Continue Board Layout
Finalize Components

Estimated time needed to work on goals for this coming week (typ. 13 hrs)

## How can we help you achieve your goals?

- Be ready for questions about components/layout

## Week 6 (9-Feb to 15-Feb) John Stinger

Goal/Task | % Done | Hours (Act.)
Driver Research | | 5
Board Development | | 3
Discussions and Meetings | | 3

Hours on task during the week (On track ≥ 13 / wk) | 11
Total hours on task so far this semester (On track ≥ 75 hrs) | 62

## Progress made during the week (Log) (What I did)

For example: Resources found (links, manuals), Designs created, Decisions made and corresponding rational, Photos of prototype progress, etc.

- The current NEMA 14 motor is rated for 4.2 V
- Looking at drivers with ~ 5 – 30 V
- Found open-source driver controllers


## Difficulties encountered during the week (What I did not do and why)

- Trying to determine the proper voltage

## Goals for this coming week (Ones that move the project forward the most)

Goal/Task | Stop Date (Est.) | Hours (Est.)
Have a specific driver chip selected | | 2
Continue with board development | | 10

Estimated time needed to work on goals for this coming week (typ. 13 hrs)

## How can we help you achieve your goals?

- Continue to be available for questions

## Week 5 (10-Feb to 16-Feb) Dale Andreoli

Goal/Task | % Done | Hours (Act.)
Create Load page | 75 | 2
Finish Home page | | 4
Remake home page according to the new design | 90 | 8

Project Objective / Mission Statements
Power Scale Dispenser:
Design, build, and test the electronics for the dispenser with a touch screen display and controlling two stepper motors by April 6, 2021 with a prototyping budget of $1000 USD and for less than 600 people-hours.

Hours on task during the week | 14
Total hours on task so far this semester | 70

## Progress made during the week (Log) (What I did)

Remade Home page according to the new design from Christian
Started Load page (old design)


## Difficulties encountered during the week (What I did not do and why)

- None

## Goals for this coming week (Ones that move the project forward the most)

Goal/Task | Stop Date (Est.) | Hours (Est.)
Implement Load screen on the new design | | 5
Implement Save screen | | 5
Collaborate with Jonathan to implement buttons from the design | | 2

Estimated time needed to work on goals for this coming week | 12

## Week 6 (9-Feb to 15-Feb) Jonathan Phillips

Goal/Task | % Done | Hours (Act.)
Front end – How to make Images into Buttons | 100 | 2
Front end – Splicing the buttons from Christian's design | 20 | 1
Front end – General Progression | | 10

Power Scale Dispenser:
Design, build, and test the electronics for the dispenser with a touch screen display and controlling two stepper motors by April 6, 2022, with a prototyping budget of $1000 USD and for less than 600 people-hours.

Hours on task during the week (On track ≥ 13 / wk) | 12
Total hours on task so far this semester (On track ≥ 75 hrs) | 65

## Progress made during the week (Log) (What I did)


## Difficulties encountered during the week (What I did not do and why)

The same button cannot raise and depress itself. It can do either or, but not both.

## Goals for this coming week (Ones that move the project forward the most)

Goal/Task | Stop Date (Est.) | Hours (Est.)
Front end – Splicing Images from Christian's design | 2/23/22 | 2
Front end – Implementation of images as buttons | 2/23/22 | 5
Front end – General Progression | 4/1/22 | 6

Estimated time needed to work on goals for this coming week (typ. 13 hrs) | 13

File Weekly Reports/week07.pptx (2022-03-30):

## Week 7 (16-Feb to 22-Feb)


## Week 7 (16-Feb to 22-Feb) Austin Stecklein

Goal/Task | % Done | Hours (Act.)
Documentation format | | 4
Backend testing | | 8

Hours on task during the week (On track ≥ 10 / wk) | 12
Total hours on task so far this semester (On track ≥ 85 hrs) | 80

## Progress made during the week (Log) (What I did)

Starting creating software and hardware documentation format. Theory, application, examples, and building on
Testing stepper dispensing
Testing PID
Testing reading from the scale

## Goals for this coming week (Ones that move the project forward the most)

Goal/Task | Stop Date (Est.) | Hours (Est.)
Continue testing with GUI and understating limitations of screen | | 8
Continue working on documentation | | 4

Estimated time needed to work on goals for this coming week (typ. 13 hrs) | 12

## Week 7 (16-Feb to 22-Feb) Colby Hatton

Goal/Task | % Done | Hours (Act.)
Schematic | 92% | 2
Layout | 18% | 9
Research/Troubleshooting | N/A | 5

Hours on task during the week (On track ≥ 10 / wk) | 16
Total hours on task so far this semester (On track ≥ 85 hrs) | ~85

## Progress made during the week (Log) (What I did)

Further work on PCB Layout. Learned multiple aspects of the layout process on KiCad.


## Difficulties encountered during the week (What I did not do and why)

- As with most PCB Software, there's a lot of unexplained behavior.
- Attempted to route the power wire unsuccessfully.

## Goals for this coming week (Ones that move the project forward the most)

Goal/Task | Stop Date (Est.) | Hours (Est.)
Layout | 2/28 | >13

Estimated time needed to work on goals for this coming week (typ. 13 hrs)

## How can we help you achieve your goals?

- Finalize parts
- Pray for me

## Week 7 (16-Feb to 22-Feb) John Stinger

Goal/Task | % Done | Hours (Act.)
Driver Research and Selection | | 5
Finding a Power Adapter | | 2
Help with Board Devel | | 3

Hours on task during the week (On track ≥ 10 / wk) | 10
Total hours on task so far this semester (On track ≥ 85 hrs) | 72

## Progress made during the week (Log) (What I did)

For example: Resources found (links, manuals), Designs created, Decisions made and corresponding rational, Photos of prototype progress, etc.

- Chose the Trinamic TM2208
- 4.75V – 36V


## Difficulties encountered during the week (What I did not do and why)

- None

## Goals for this coming week (Ones that move the project forward the most)

Goal/Task | Stop Date (Est.) | Hours (Est.)
Continue Board Development | | 10+
Resolve operating voltage | | 3

Estimated time needed to work on goals for this coming week (typ. 13 hrs) | 13+

## How can we help you achieve your goals?

- Continue to be available for reference.

## Week 7 (16-Feb to 22-Feb) - Dale Andreoli

Goal/Task | % Done | Hours (Act.)
Implement Load screen on the new design | 90 | 2
Implement Save screen | 60 | 6
Implement Settings screen | 60 | 5

Project Objective / Mission Statements
Power Scale Dispenser:
Design, build, and test the electronics for the dispenser with a touch screen display and controlling two stepper motors by April 6, 2021 with a prototyping budget of $1000 USD and for less than 600 people-hours.

Hours on task during the week | 13
Total hours on task so far this semester | 83

## Progress made during the week (Log) (What I did)

Started Settings page
Started Save page
Load page is now working


## Difficulties encountered during the week (What I did not do and why)

- Learning the UI library as I go

## Goals for this coming week (Ones that move the project forward the most)

Goal/Task | Stop Date (Est.) | Hours (Est.)
Finish Save screen | | 4
Finish Settings screen and sub screens | | 7
Collaborate with Jonathan to get images in the design | | 2
Collaborate with Austin to ensure UI and back-end can communicate | | 1

Estimated time needed to work on goals for this coming week | 14

## Week 7 (16-Feb to 22-Feb) Jonathan Phillips

Goal/Task | % Done | Hours (Act.)
Front end – Implementation of images as buttons | 80 | 4
Front end Meeting | 100 | 1
Front end – General Progression | N/A | 5

Hours on task during the week (On track ≥ 10 / wk) | 10
Total hours on task so far this semester (On track ≥ 85 hrs) | 75

## Progress made during the week (Log) (What I did)


## Difficulties encountered during the week (What I did not do and why)

- Exact Sizing of the Images on Screen

## Goals for this coming week (Ones that move the project forward the most)

Goal/Task | Stop Date (Est.) | Hours (Est.)
Front End – Implementation of Images as Buttons | 3/1/22 | 3
Front End – Working on the other Pages
Front End – General Progression | 4/6/22

Estimated time needed to work on goals for this coming week (typ. 13 hrs) | 13

## How can we help you achieve your goals?

- Keep on Keeping on

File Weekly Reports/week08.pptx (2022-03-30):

## Week 8 (23-Feb to 1-Mar)


## Week 8 (23-Feb to 1-Mar) Austin Stecklein

Goal/Task | % Done | Hours (Act.)
Merge backend & frontend | 10 | 5
Testing backend | 98 | 5
Ubuntu configuration | 50 | 16

Hours on task during the week (On track ≥ 13 / wk) | 16
Total hours on task so far this semester (On track ≥ 98 hrs) | 96

## Progress made during the week (Log) (What I did)

Starting testing frontend on Beaglebone black
Finishing testing of backend with each process running on sperate threads
Configuring Ubuntu to function as desired. (i.e. auto start application, downloading libraries, and security config)

## Difficulties encountered during the week (What I did not do and why)

- Ubuntu configuration
- Graphic operating system not running

## Goals for this coming week (Ones that move the project forward the most)

Goal/Task | Stop Date (Est.) | Hours (Est.)
Get graphic operating system to run | 3/9 | 2-4
Start testing Frontend | 3/9 | 5
linking frontend and backend functionality | 3/15 | 6

Estimated time needed to work on goals for this coming week (typ. 13 hrs) | 13

## Week 8 (23-Feb to 1-Mar) Colby Hatton

Goal/Task | % Done | Hours (Act.)
PCB Layout | 80% | 15

Hours on task during the week (On track ≥ 13 / wk) | 16
Total hours on task so far this semester (On track ≥ 98 hrs)

## Progress made during the week (Log) (What I did)

Laid out and routed nearly the entire board. Power components are all that remains.

Before

After


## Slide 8


## Difficulties encountered during the week (What I did not do and why)

- Ran out of Audiobook. Routing takes a long time.

## Goals for this coming week (Ones that move the project forward the most)

Goal/Task | Stop Date (Est.) | Hours (Est.)
Route Power components. | 3/9 | 5
Determine how to split project across multiple accounts | 3/3 | 1

Estimated time needed to work on goals for this coming week (typ. 13 hrs)

## How can we help you achieve your goals?

- Be ready to answer questions about lines, signals, and pins.

## Week 8 (23-Feb to 1-Mar) John Stinger

Goal/Task | % Done | Hours (Act.)
Board Development | 80% | 6
Price Estimate | 100% | 2
Other | | 3

Hours on task during the week (On track ≥ 13 / wk) | 11
Total hours on task so far this semester (On track ≥ 98 hrs) | 83

## Progress made during the week (Log) (What I did)

For example: Resources found (links, manuals), Designs created, Decisions made and corresponding rational, Photos of prototype progress, etc.

- Helped develop the board
- Made a price estimate for the project

## Difficulties encountered during the week (What I did not do and why)

- Most of the components are going to be in the board cost

## Goals for this coming week (Ones that move the project forward the most)

Goal/Task | Stop Date (Est.) | Hours (Est.)
Continue Board Development | | 10

Estimated time needed to work on goals for this coming week (typ. 13 hrs)

## Week 8 (23-Feb to 1-Mar) Johnathan Philips

Goal/Task | % Done | Hours (Act.)
Front End – Implementation of Images as Buttons | 95 | 2
Front End – Working on the other Pages | 42 | 5
Front End – General Progression | N/A | 2

Hours on task during the week (On track ≥ 13 / wk) | 11
Total hours on task so far this semester (On track ≥ 98 hrs) | 86

## Progress made during the week (Log) (What I did)


## Difficulties encountered during the week (What I did not do and why)

- Receiving input from user and storing new value

## Goals for this coming week (Ones that move the project forward the most)

Goal/Task | Stop Date (Est.) | Hours (Est.)
Front End – Save Card Screen and Unit Change on Home Screen | 3/9/22 | 7
Front End – Receiving input from user | 3/9/22 | 4
Front End – General Progression | 4/6/22 | 2

Estimated time needed to work on goals for this coming week (typ. 13 hrs) | 13

## Week8 (23-Feb to 1-Mar) - Dale Andreoli

Goal/Task | % Done | Hours (Act.)
Finish Save screen skeleton | 100 | 4
Finish Settings screen and sub screens skeletons | 100 | 7
Implement Pages in the Load screen | | 2

Project Objective / Mission Statements
Power Scale Dispenser:
Design, build, and test the electronics for the dispenser with a touch screen display and controlling two stepper motors by April 6, 2021 with a prototyping budget of $1000 USD and for less than 600 people-hours.

Hours on task during the week | 13
Total hours on task so far this semester | 96

## Progress made during the week (Log) (What I did)


Finished settings pages
- Brightness/sound, Feed Adjustments, Default
Finished Save page
Started making pages for the
Load screen


## Difficulties encountered during the week (What I did not do and why)

- What should be happening in the Scale Config page?


## Goals for this coming week (Ones that move the project forward the most)

Goal/Task | Stop Date (Est.) | Hours (Est.)
Collaborate with Jonathan and Austin – connect UI to backend – get UI looking as designed | | 3
Finish Load screen pages module | | 6
Start View page once a similar solution is arrived at in the Load page | | 4

Estimated time needed to work on goals for this coming week | 13

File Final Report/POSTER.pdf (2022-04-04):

# Powder Scale and Dispenser

Abstract | Project Description

# Results

## ECEN 499 | Senior Project – Winter 2022

### Austin Stecklein, Colby Hatton, Dale Andreoli, John Stinger, Jonathan Phillips

Creedmoor is a sporting company that has specialized in precision firearm products since 1979. We were approached by Creedmoor and had the opportunity to help them in their quest for excellence by designing a brand-new product. The goal was to create an automatic powder dispenser with a fully integrated, touch-screen GUI that could communicate with a digital scale to ensure the easiest and most precise reloading experience.

Immediately, we divided the project into two categories: hardware and software. The software was then subdivided into frontend and backend. The frontend covered the touchscreen layout and interface, while the backend focused on machine level programing to support an operating system and to allow the touchscreen, the powder dispenser, and the scale to all work together.
The hardware world consisted of designing an entirely new circuit board that could both operate everything mentioned already as well as being ready as a prototype for a commercial product. This included the redesign of a BeagleBone board and the full integration of motor drivers for the dispenser.

While all the goals were not achieved within the timeframe of the semester, amazing progress was made. The circuit board was fully designed. Communications between a stand-in BeagleBone, the touchscreen, and the scale was a success. The final board design did not come to fruition as there is still a shortage of electronic components. Yet, more importantly, we all grew as individuals and as a group.



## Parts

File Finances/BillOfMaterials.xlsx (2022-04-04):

Names of Team Members:
Item # | Date Ordered | Date Received | Part Description | Part # (Mfr) | Manufacturer | Qty | Unit Price | Total Cost | P/N-1st Dist. | Link-1st Distributor | P/N-2nd Dist. (Optional) | Link-2nd Distributor (optional) | Notes:
1 | 2022-01-26 | 2022-01-29 | Geeek Pi 5 Inch 800 X 400 LCD display | EP-0081 | Geeekpi | 1 | $59.99 | $63.59 | EP-0081 | https://www.amazon.com/GeeekPi-Capacitive-800x480-Raspberry-BeagleBone/dp/B0749D617J?hvadid=232527108212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 | 8548900030 | https://www.seeedstudio.com/5-inch-800x480-Capacitive-TouchScreen.html
2 | 2022-01-31 | 2022-02-05 | BeagleBone Black wireless BBONE-BLACK | 8541611738 | embest | 1 | $99.99 | $105.99 | 8541611738 | https://www.amazon.com/BeagleBone-Black-Single-Computer-Development/dp/B00LC1924G
3 |  |  | Vibration ERM MTR 13000 RPM 3V | ROB-08449 | SparkFun Electronic | 1 | $2.15 | $2.15 | ROB-08449-ND | https://www.digikey.com/en/products/detail/sparkfun-electronics/ROB-08449/7393691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 | 474-ROB-08449 | https://www.mouser.com/ProductDetail/SparkFun/ROB-08449?qs=WyAARYrbSnZj6jJCAHtRrQ%3D%3D
4 |  |  | Speaker, 93DB SENSITIVITY, 15mm | SP-1504-18 | Soberton Inc. | 1 | $2.37 | $2.37 | 433-1239-ND | https://www.digikey.com/en/products/detail/soberton-inc/SP-1504-18/9924400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 | 253-AK1508EA15C3 | https://www.mouser.com/ProductDetail/AATC/AK-1508EA-15C3?qs=uwxL4vQweFOdvezzr69VFQ%3D%3D
5 |  |  | CONN HEADER R/A 2POS 2.5mm | S2B-XH-A(LF)(SN) | JST Sales America Inc. | 2 | $0.18 | $0.36 | 455-2257-ND | https://www.digikey.com/en/products/detail/jst-sales-america-inc/S2B-XH-A-LF-SN/1651055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
6 |  |  | CON HEADER SMD 4POS 2MM | B4B-PH-SM4-TB(LF)(SN) | JST Sales America Inc. | 2 | $0.75 | $1.50 | 455-1736-1-ND | https://www.digikey.com/en/products/detail/jst-sales-america-inc/B4B-PH-SM4-TB-LF-SN/926643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
7 |  |  | CONN SOCKET 4POS IDC 26AWG TIN | 04KR-D6S-P | JST Sales America Inc. | 2 | $0.51 | $1.02 | 455-2676-ND | https://www.digikey.com/en/products/detail/jst-sales-america-inc/04KR-D6S-P/2797505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
8 |  |  |  |  |  |  |  | $0.00
9 |  |  |  |  |  |  |  | $0.00
10 |  |  |  |  |  |  |  | $0.00
11 |  |  |  |  |  |  |  | $0.00
12 |  |  |  |  |  |  |  | $0.00
13 |  |  |  |  |  |  |  | $0.00
14 |  |  |  |  |  |  |  | $0.00
15 |  |  |  |  |  |  |  | $0.00
16 |  |  |  |  |  |  |  | $0.00
17 |  |  |  |  |  |  |  | $0.00
18 |  |  |  |  |  |  |  | $0.00
19 |  |  |  |  |  |  |  | $0.00
20 |  |  |  |  |  |  |  | $0.00
21 |  |  |  |  |  |  |  | $0.00
22 |  |  |  |  |  |  |  | $0.00
23 |  |  |  |  |  |  |  | $0.00
24 |  |  |  |  |  |  |  | $0.00
25 |  |  |  |  |  |  |  | $0.00
26 |  |  |  |  |  |  |  | $0.00
27 |  |  |  |  |  |  |  | $0.00
28 |  |  |  |  |  |  |  | $0.00

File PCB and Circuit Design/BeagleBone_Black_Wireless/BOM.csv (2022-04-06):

Reference | Value | JLCPCB PN
C1 | 18pF, 50V
C10 | 47pF, 6.3V
C11 | 47pF, 6.3V | C1567
C12 | 47pF, 6.3V
C13 | 47pF, 6.3V
C14 | 47pF, 6.3V
C15 | 10uF
C16 | 47pF, 6.3V
C17 | 100nF
C18 | 47pF, 6.3V
C19 | 22nF
C2 | 18pF, 50V
C20 | 47pF, 6.3V
C21 | 100nF
C22 | .1uF, 6.3V
C23 | 47pF, 6.3V
C24 | 100nF
C25 | 2.2uF, 6.3V
C26 | 47pF, 6.3V
C27 | 100uF
C28 | .1uF, 6.3V
C29 | 47pF, 6.3V
C3 | 18pF, 50V
C30 | 2.2uF, 6.3V
C31 | .1uF, 6.3V
C32 | 2.2uF, 6.3V
C33 | .1uF, 6.3V
C34 | 2.2uF, 6.3V
C35 | 10uF
C36 | 100nF
C37 | 22nF
C38 | .1uF, 6.3V
C39 | 100nF
C4 | 18pF, 50V
C40 | 100nF
C41 | 100uF
C42 | 2.2uF, 6.3V
C43 | .1uF, 6.3V
C44 | 220uF 6.3V
C45 | .1uF, 6.3V
C46 | 10uF,10V
C47 | .1uF, 6.3V
C48 | .1uF, 6.3V
C49 | .1uF, 6.3V
C5 | 47pF, 6.3V
C6 | 47pF, 6.3V
C7 | 47pF, 6.3V
C8 | 47pF, 6.3V
C9 | 47pF, 6.3V
D1 | RB751V40,115
F1 | 1206L025YR
FB1 | 2.5k Ohm (BLM18BD252SN1D)
FB2 | 1k BLM15AG102SN1D
FB3 | 1k BLM15AG102SN1D
FB4 | 1k BLM15AG102SN1D
FB5 | 0.1 Ohm, 0805
FB6 | 150 Ohm 800mA
FUD1 | FIDUCIAL
FUD2 | FIDUCIAL
FUD3 | FIDUCIAL
FUD4 | FIDUCIAL
FUD5 | FIDUCIAL
FUD6 | FIDUCIAL
IC1 | OSD3358
IC10 | TPD4S012DRY
IC11 | TLVH431 (SOT-23-3)
IC12 | DNP TLVH431 (SOT-23-3)
IC2 | SN74LVC1G07DCK
IC3 | TDA19988BHN/C1,557
IC4 | SN74AUC1G74
IC5 | IP4283CZ10-TBR
IC6 | IP4283CZ10-TBR
IC7 | TPS2051BDGN
IC8 | TPD4S012DRY
IC9 | 24LC32AT-I/OT
J3 | BG125-10-A-1-1-0440-N-D
MGT1 | MOUNTING_HOLE
MGT2 | MOUNTING_HOLE
MGT3 | MOUNTING_HOLE
MGT4 | MOUNTING_HOLE
OSC1 | ASDMB-24.576MHZ-LC-T
P1 | B2B-PH-SM4-TB
P2 | B2B-PH-SM4-TB
PWR1 | LTST-C191TBKT
Q1 | 32.768kHz
Q2 | 24 MHz
R1 | 0.11
R10 | 0, 1%
R11 | 1.5k, 1%
R12 | 1.5k, 1%
R13 | 10k, 1%
R14 | 33
R15 | 10k, 1%
R16 | 10k, 1%
R17 | 0, 1%
R18 | 4.75k, 1%
R19 | 4.75k, 1%
R2 | 0.11
R20 | 0, 1%
R21 | 0, 1%
R22 | 10k, 1%
R23 | 10k, 1%
R24 | 10k, 1%
R25 | 10k, 1%
R26 | 100k, 1%
R27 | 10k, 1%
R28 | 100k, 1%
R29 | 100k, 1%
R3 | DNP 1M, 1%
R30 | 10k, 1%
R31 | 100k, 1%
R32 | 10k, 1%
R33 | 100k, 1%
R34 | 100k, 1%
R35 | 100k, 1% | C25086
R36 | 22
R37 | 0, 1%
R38 | 0, 1%
R39 | 0, 1%
R4 | 1M, 1%
R40 | 0, 1%
R41 | 0, 1%
R42 | 100k, 1%
R43 | 100k, 1%
R44 | 100k, 1%
R45 | 100k, 1%
R46 | 100k, 1%
R47 | 100k, 1%
R48 | 100k, 1%
R49 | 100k, 1%
R5 | 0.11
R50 | 100k, 1%
R51 | .1, R0805
R52 | 1.5k, 1%
R53 | 1.5k, 1%
R54 | 10k, 1%
R55 | 4.75k, 1%
R56 | 499
R57 | DNP
R58 | 10k 1%
R59 | 40.2k 1%
R6 | 0.11
R60 | 10k, 1%
R61 | 1k
R62 | 1k
R63 | 1k
R64 | 1k
R65 | DNP 499
R66 | DNP
R67 | DNP 10k 1%
R68 | DNP 40.2k 1%
R7 | 10k, 1%
R8 | 0, 1%
R9 | 27k, 1%
RESET1 | MINI_PUSHBUTTON
T1 | MMBT2907
T2 | DNP MMBT2907
TP1 | TESTPAD_W_HOLE_1X1
TP2 | TESTPAD_W_HOLE_1X1
TP3 | TESTPAD_W_HOLE_1X1
TP4 | TESTPAD_W_HOLE_1X1
TP5 | TESTPAD_W_HOLE_1X1
TP6 | TESTPAD_W_HOLE_1X1
TP7 | TESTPAD_W_HOLE_1X1
TP8 | TESTPAD_W_HOLE_1X1
U1 | TMC2208-LA-T
U2 | TMC2208-LA-T
USR1 | LTST-C191TBKT
USR2 | LTST-C191TBKT
USR3 | LTST-C191TBKT
USR4 | LTST-C191TBKT
X1 | 10118241-001RLF
X2 | USB_HOST_W_CHASSIS_GND
X3 | SCHA5B0200
X4 | PJ-102B
X5 | 10118192-0001LF

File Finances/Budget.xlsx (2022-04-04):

Item | Total cost
GEEEK Pi 5 inch 800 x 400 | $163.59
parts for BeagleBone | $15.05
Beaglebone Black wireless (Returned) | $105.99
total | $178.64

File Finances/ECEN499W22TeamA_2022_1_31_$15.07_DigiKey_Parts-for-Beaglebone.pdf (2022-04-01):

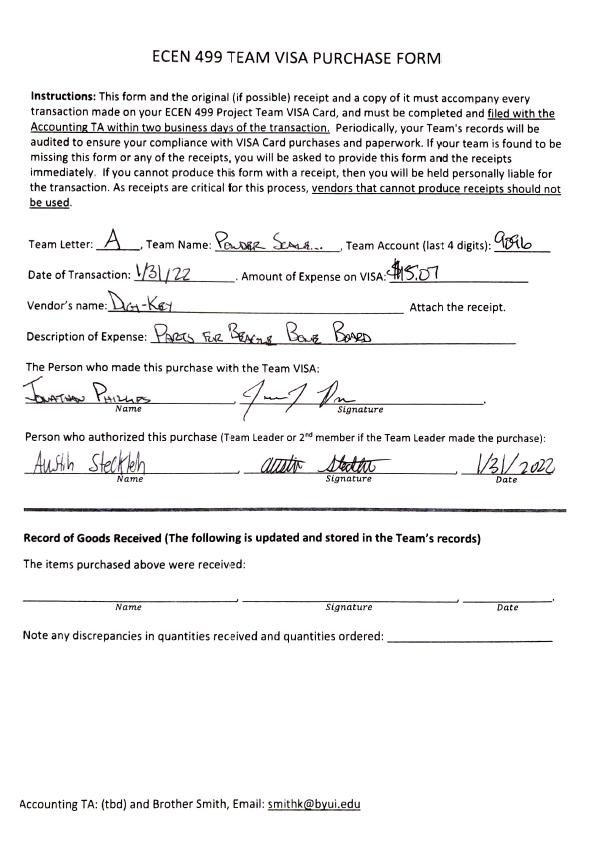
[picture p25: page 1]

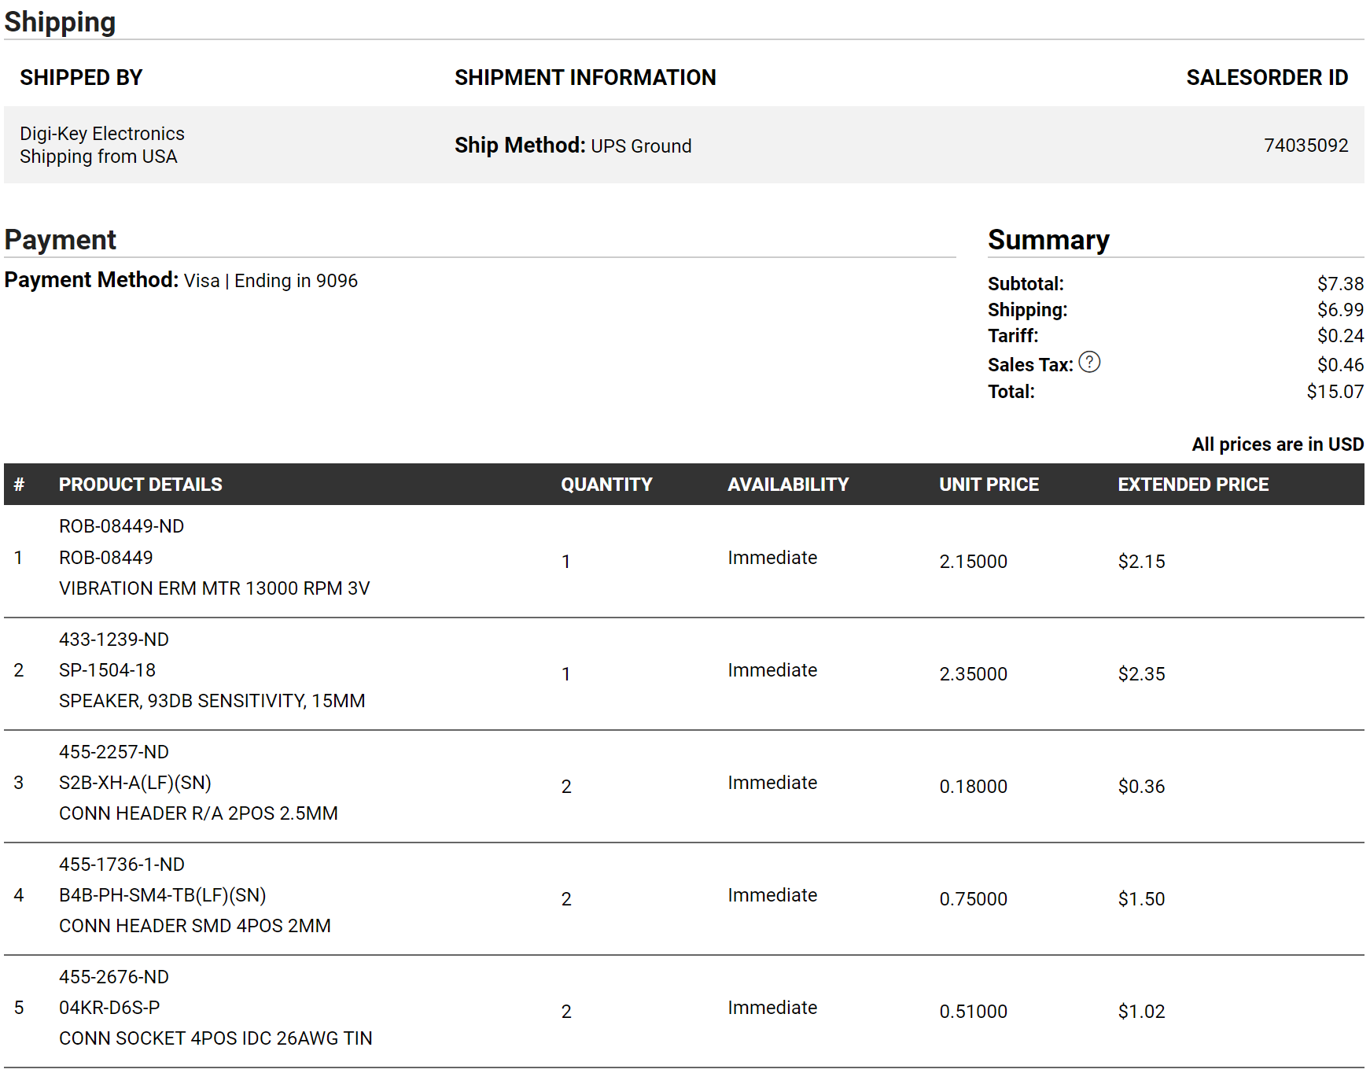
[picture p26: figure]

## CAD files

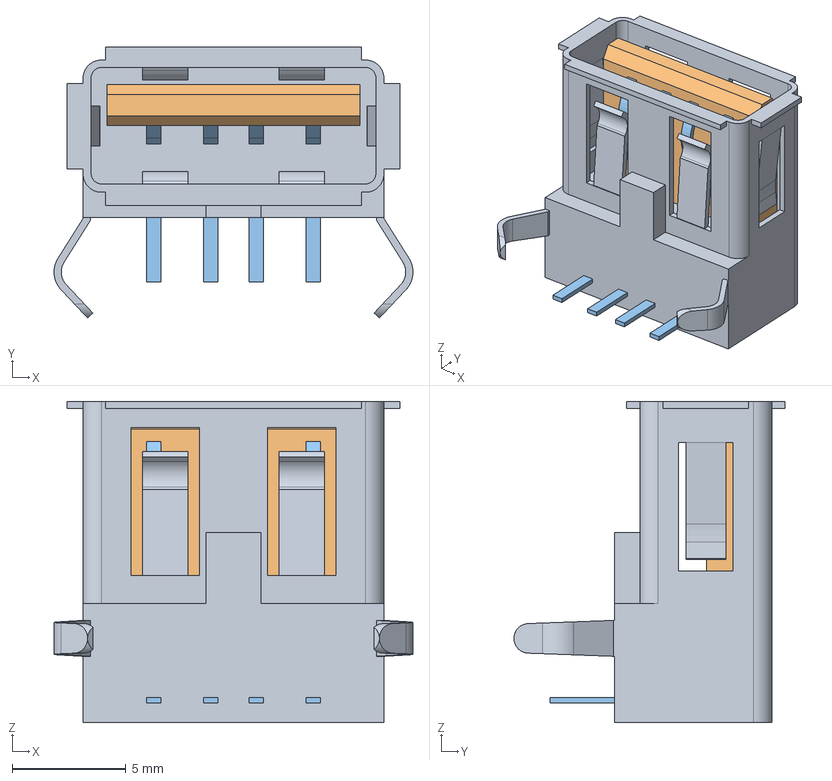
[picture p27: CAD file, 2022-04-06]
PCB and Circuit Design/BeagleBone_Black_Wireless/3D Models/USB-A-S-F-W-TH.stp
15.7 x 11.9 x 14.1 mm
_USB-A-S-TH_S
_USB-A-S-W-TH_B
_USB-A-S-TH_P

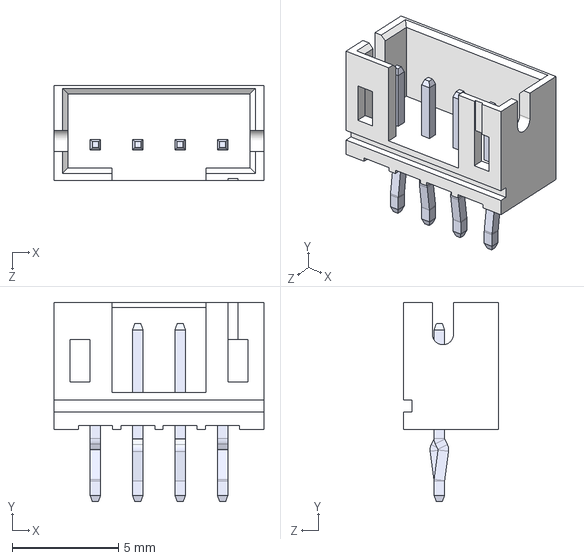
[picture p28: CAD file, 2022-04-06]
PCB and Circuit Design/BeagleBone_Black_Wireless/B4B-PH-K-S_LF__SN_/B4B-PH-K-S_LF__SN_.step
9.90 x 9.40 x 4.50 mm

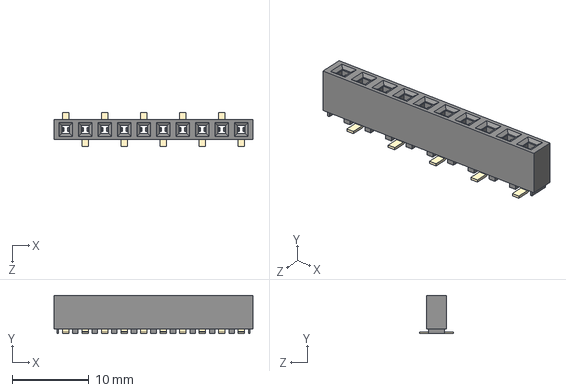
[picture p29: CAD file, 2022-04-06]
PCB and Circuit Design/BeagleBone_Black_Wireless/BG125-10-A-1-1-0440-N-D/BG125-10-A-1-1-0440-N-D.step
25.9 x 5.00 x 4.40 mm

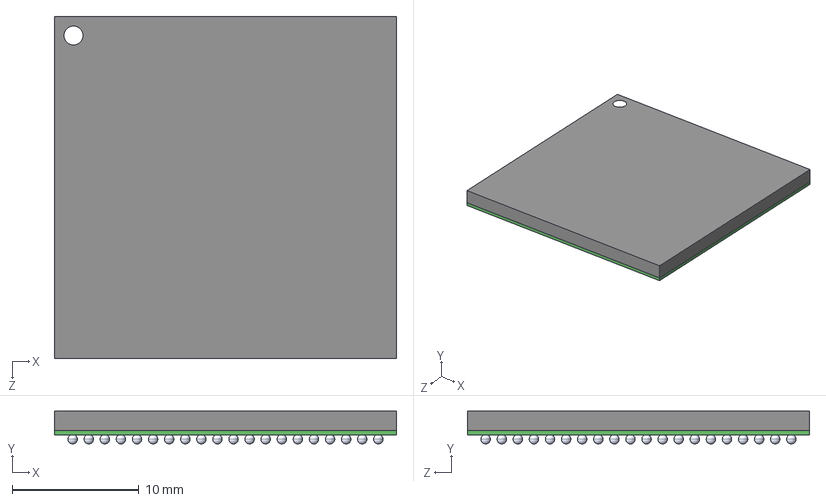
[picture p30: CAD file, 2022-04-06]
PCB and Circuit Design/BeagleBone_Black_Wireless/OSD3358-512M-IND.STEP
27.0 x 2.60 x 27.0 mm

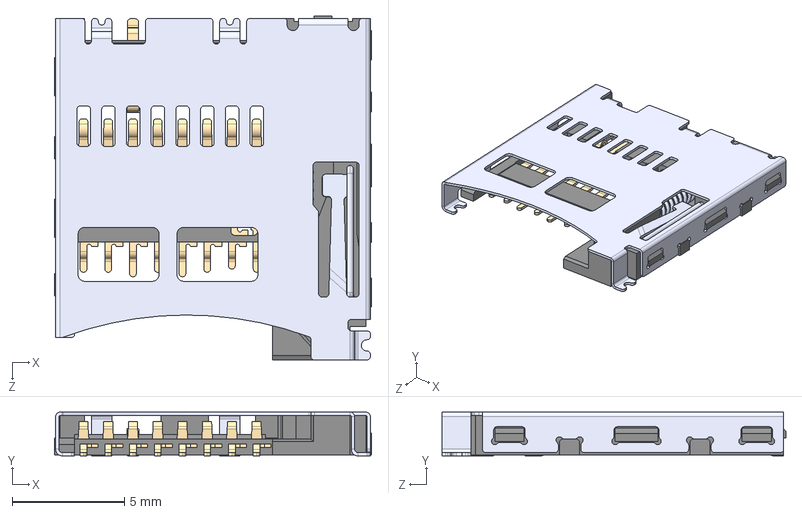
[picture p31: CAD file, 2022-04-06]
PCB and Circuit Design/BeagleBone_Black_Wireless/3D Models/MEM2051-00-195-00-A--3DModel-STEP-1.STEP
14.1 x 1.95 x 15.3 mm

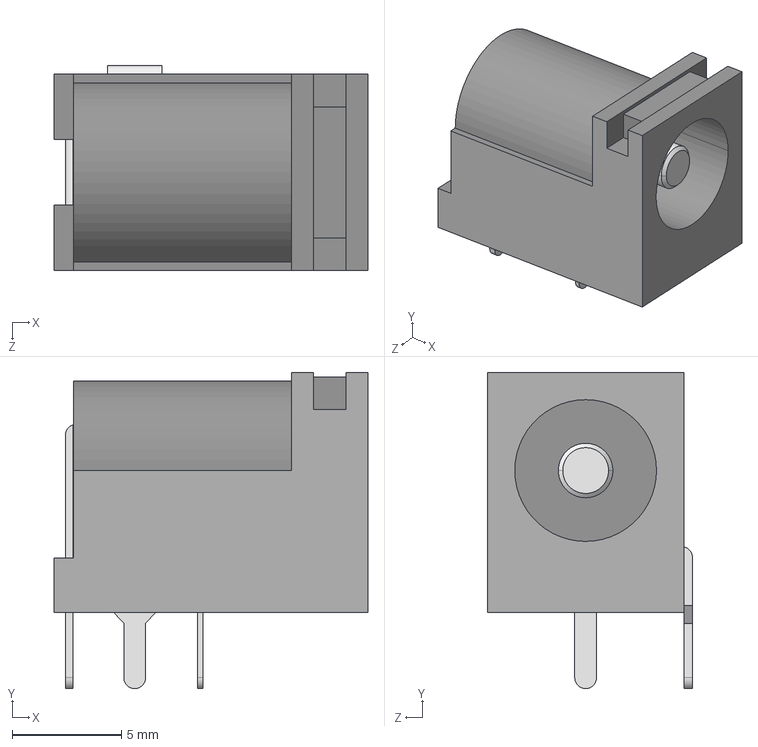
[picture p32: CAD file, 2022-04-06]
PCB and Circuit Design/BeagleBone_Black_Wireless/3D Models/CUI_DEVICES_PJ-102B.step
14.4 x 14.5 x 9.40 mm

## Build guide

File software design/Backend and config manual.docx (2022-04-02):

# Setting up the Beagle Bone with blank SD card

1. Insert SD card into SD card slot (must be 8GB or higher) with the AM3358 Debian 10.3 2020-04-06 4GB SD IoT operating system image installed.
2. Press and hold the user button before plugging in the board and wait until all four LED lights turn on.
3. Connect to the board VIA cloud9 IDE interface (http://192.168.7.2:3000). This usually takes time to connect so be patient with the board.
4. Once you are in the IDE open a terminal.
5. Either connect the board through ethernet or WIFI. Steps for connecting are found here https://beagleboard.org/upgrade
6. Run the following commands
  a. cd /opt/scripts
  b. git pull
  c. sudo tools/update_kernel.sh
    i. When asked for password the default is set to “temppwd”
  d. sudo shutdown -r now
7. Turn the Beaglebone back on and run the following commands
  a. sudo apt update
  b. sudo apt upgrade
  c. y
  d. sudo apt install -y ti-tidl mjpg-streamer-opencv-python
  e. sudo /opt/scripts/tools/version.sh
  f. apt-get install python-tk
  g. sudo apt-get -y install lxde lxde-core lxde-icon-theme
8. Restart the Beaglebone with the HDMI plugin to the beaglebone and you should see the LXDE display popup. The login is username:debain and password: temppwd.
9. Open a terminal and do a “git clone dispenser repo” to then download the code to the beagleBone.
10. Run the “main.py” file with the command “python3 main.py”

# Hardware connection setup for Beagle Bone black prototype

Beagle pin | connection
P8_19 | Angle step
P8_7 | Angle Dir
P8_9 | Angle Slp
P8_15 | Angle MS1
P8_17 | Angle MS2
P8_8 | Angle Ena
P8_13 | Trickle Step
P8_10 | Trickle Dir
P8_12 | Trickle Slp
P8_14 | Trickle MS1
P8_16 | Trickle MS2
P8_26 | Trickle Ena
DGND | acc GND
P9_40 | Read Angle
P8_27 | LCD_VSYNC
P8_29 | LCD_HSYNC
P8_31 | LCD_DATA14
P8_33 | LCD_DATA13
P8_35 | LCD_DATA12
P8_37 | LCD_DATA8
P8_39 | LCD_DATA6
P8_41 | LCD_DATA4
P8_43 | LCD_DATA2
P8_45 | LCD_DATA0
P8_28 | LCD_PCLK
P8_30 | LCD_AC_BIAS
P8_32 | LCD_DATA15
P8_34 | LCD_DATA11
P8_36 | LCD_DATA10
P8_38 | LCD_DATA9
P8_40 | LCD_DATA7
P8_42 | LCD_DATA5
P8_44 | LCD_DATA3
P8_46 | LCD_DATA1
DGND | Speaker Gnd
P9_22 | Speaker output
DGND | Haptic GND
P9_24 | Haptic

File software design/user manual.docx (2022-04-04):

# User manual

# Homepage

Once the program starts the homepage is split into two sections. The numpad is on the left and the scale data and controls on the right. The numpad on the left is used to set the value of the target weight. The value of the target weight will update below the scale value. To change units to match the scale click on the unit’s tab and select the desired unit. There are three buttons below the target weight value that allow for manual control over the barrel. The fastest speed being coarse and the slowest being bump.

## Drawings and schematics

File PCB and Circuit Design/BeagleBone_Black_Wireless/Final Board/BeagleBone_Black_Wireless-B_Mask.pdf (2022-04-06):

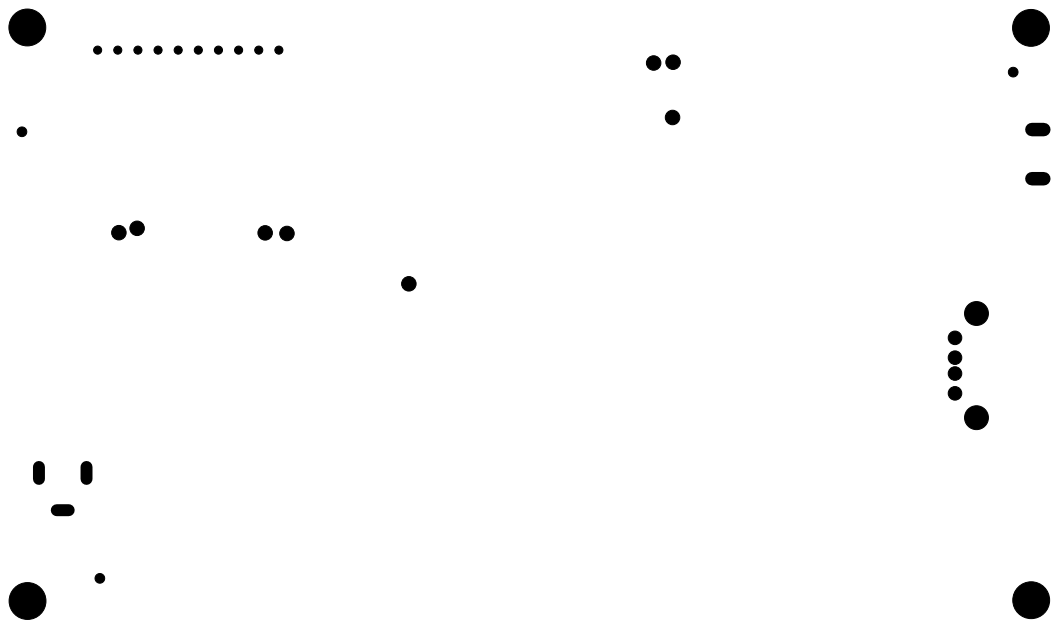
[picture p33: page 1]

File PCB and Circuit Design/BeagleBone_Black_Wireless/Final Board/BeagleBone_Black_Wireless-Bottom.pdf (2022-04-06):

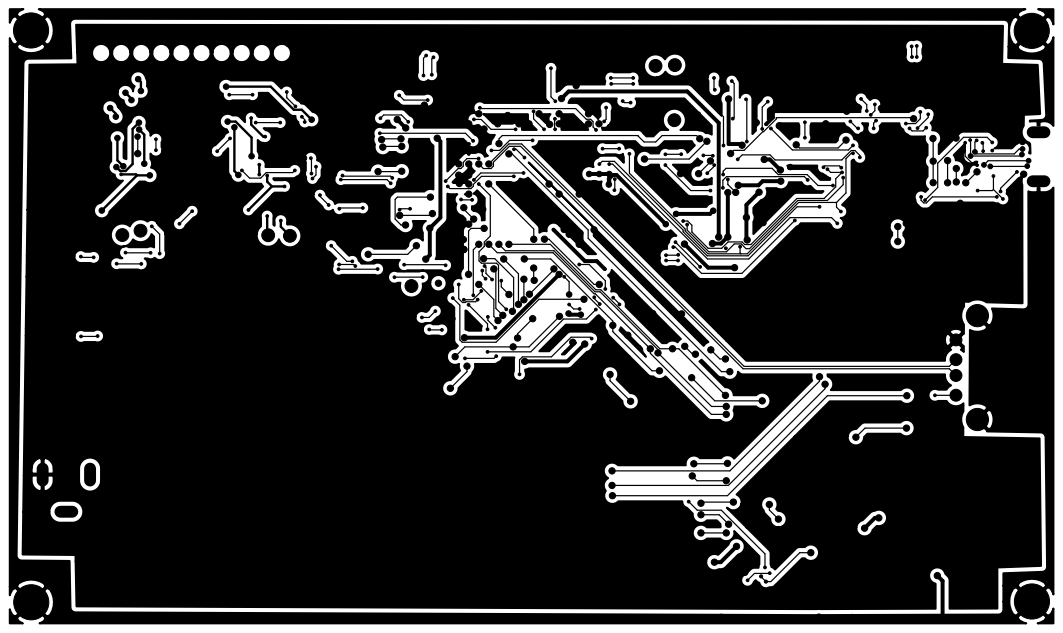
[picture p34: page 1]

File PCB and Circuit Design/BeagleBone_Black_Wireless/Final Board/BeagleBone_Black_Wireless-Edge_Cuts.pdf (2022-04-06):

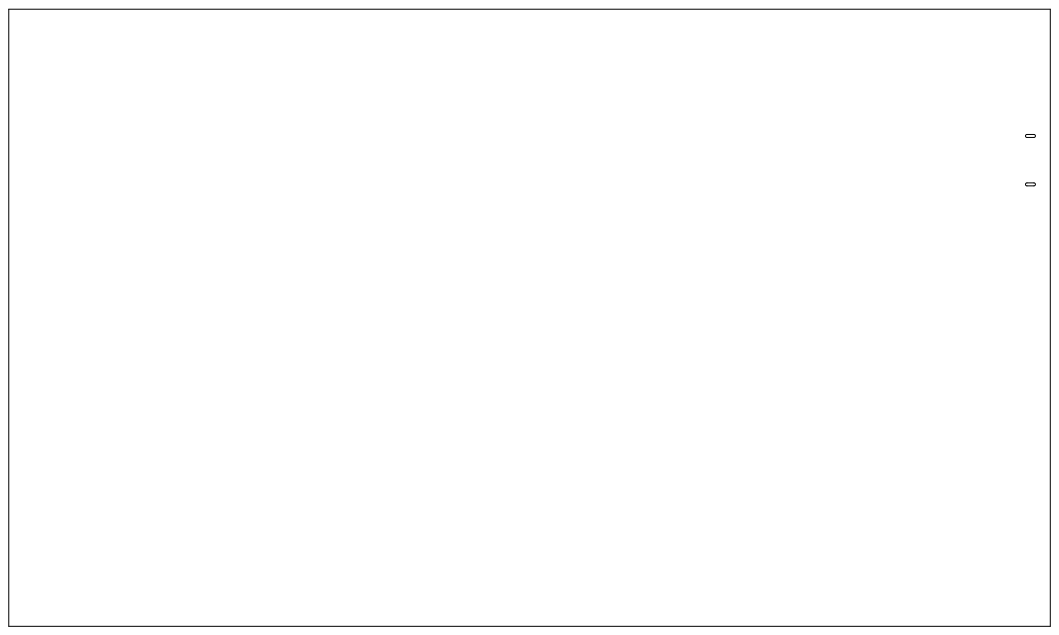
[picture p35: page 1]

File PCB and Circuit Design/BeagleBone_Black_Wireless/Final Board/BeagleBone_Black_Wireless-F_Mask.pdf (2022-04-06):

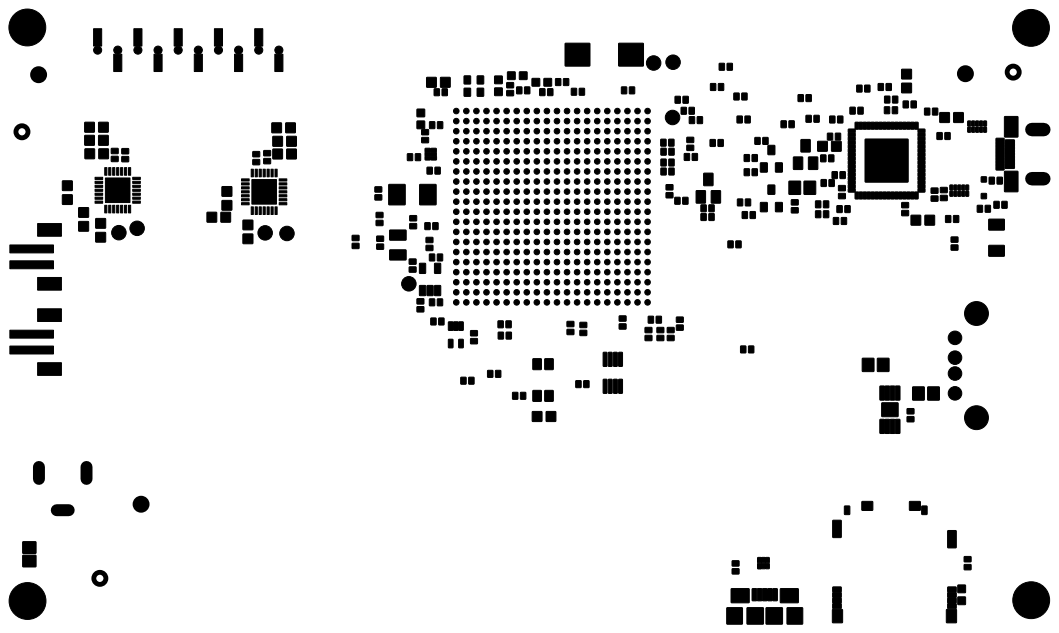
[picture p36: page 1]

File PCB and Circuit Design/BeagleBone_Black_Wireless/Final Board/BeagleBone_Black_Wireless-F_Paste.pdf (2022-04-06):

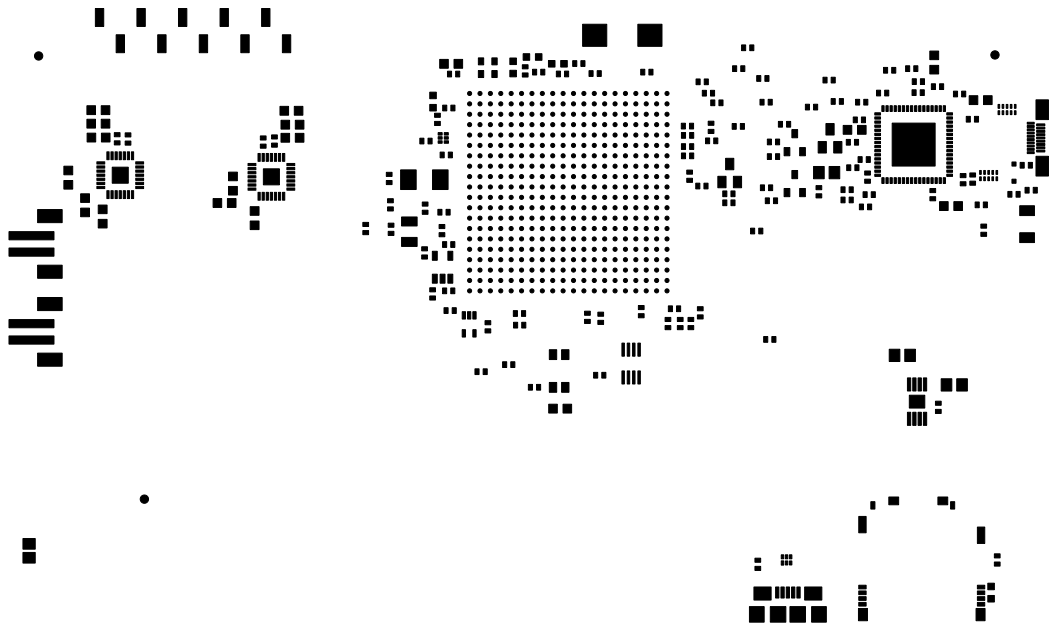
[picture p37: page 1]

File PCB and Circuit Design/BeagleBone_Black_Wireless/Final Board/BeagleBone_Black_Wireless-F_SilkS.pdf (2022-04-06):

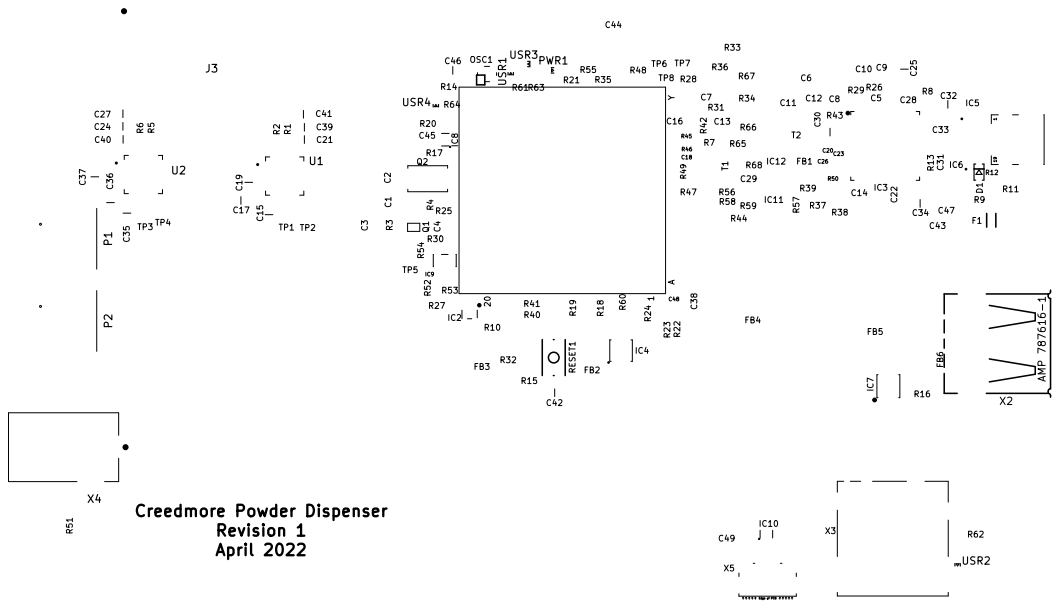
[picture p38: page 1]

Creedmore Powder Dispenser Revision 1 April 2022

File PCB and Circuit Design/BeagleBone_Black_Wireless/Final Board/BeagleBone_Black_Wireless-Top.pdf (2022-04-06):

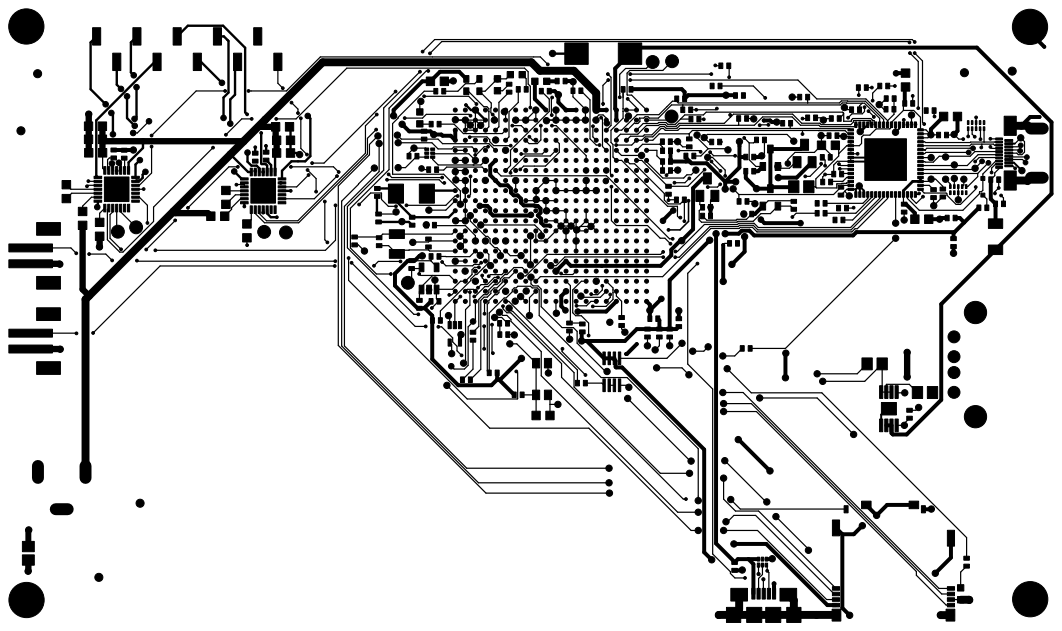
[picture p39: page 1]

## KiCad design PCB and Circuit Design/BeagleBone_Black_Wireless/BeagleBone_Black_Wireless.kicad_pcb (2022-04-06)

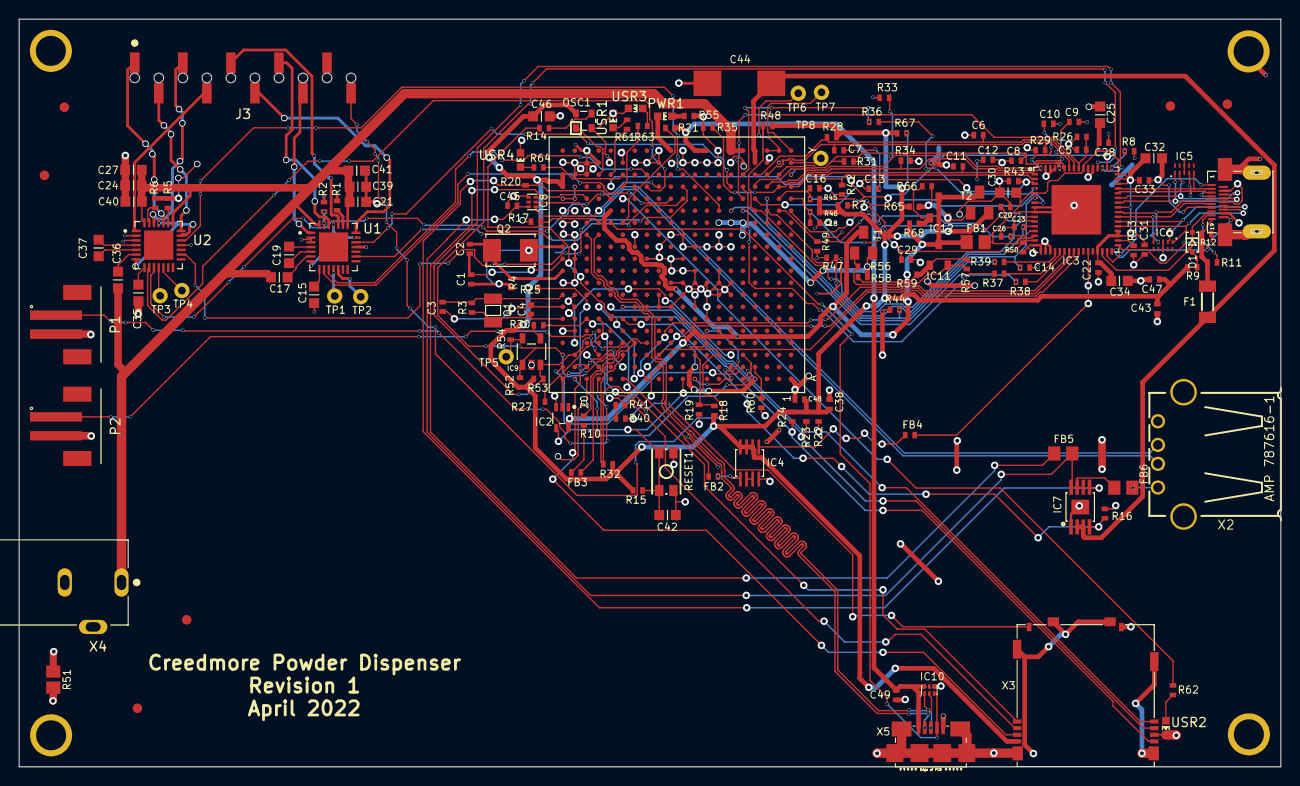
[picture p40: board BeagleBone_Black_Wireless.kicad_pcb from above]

Board: 2 copper layers, 133.4 x 79.0 mm, 176 parts (0 on the bottom side), 159 nets.

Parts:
C1, C2, C3, C4: 18pF, 50V; C0402K
C5, C6, C7, C8, C9, C10, C11, C12, C13, C14, C16, C18, C20, C23, C26, C29: 47pF, 6.3V; C0402K
C15, C35: 10uF; C0603K
C17, C21, C24, C36, C39, C40: 100nF; C0603K
C19, C37: 22nF; C0603K
C22, C28, C31, C33, C38, C43, C45, C47, C48, C49: .1uF, 6.3V; C0402K
C25, C30, C32, C34, C42: 2.2uF, 6.3V; C0603K
C27, C41: 100uF; C0603K
C44: 220uF 6.3V; D_7343-31W
C46: 10uF,10V; C0603K
D1: RB751V40,115; SOD323(NXP)REFLOW
F1: 1206L025YR; SM-1206
FB1: 2.5k Ohm (BLM18BD252SN1D); 0805-RESISTOR
FB2, FB3, FB4: 1k BLM15AG102SN1D; R0402
FB5: 0.1 Ohm, 0805; 0805-RESISTOR
FB6: 150 Ohm 800mA; 0805-RESISTOR
FUD1, FUD2, FUD3, FUD4, FUD5, FUD6: FIDUCIAL; FIDUCIAL_40MIL
IC1: OSD3358
IC2: SN74LVC1G07DCK; SC70(TI-DCK)
IC3: TDA19988BHN/C1,557; SOT804-4(NXP)
IC4: SN74AUC1G74; SM8-8(TI)
IC5, IC6: IP4283CZ10-TBR; SOT1176-1(NXP)
IC7: TPS2051BDGN; MSOP-POWER.PAD-8(TI)
IC8, IC10: TPD4S012DRY; SON-6(TI)-DRY
IC9: 24LC32AT-I/OT; SOT23-5(MICROCHIP)
IC11: TLVH431 (SOT-23-3); DBZ_R-PDSO-G3
IC12: DNP TLVH431 (SOT-23-3); DBZ_R-PDSO-G3
J3: BG125-10-A-1-1-0440-N-D; GCT_BG125-10-A-1-1-0440-N-D
MGT1, MGT2, MGT3, MGT4: MOUNTING_HOLE
OSC1: ASDMB-24.576MHZ-LC-T; OSCILLATOR-2.5X2.0-BBB
P1, P2: B2B-PH-SM4-TB; JST_B2B-PH-SM4-TB
PWR1: LTST-C191TBKT; 0603-LED
Q1: 32.768kHz; CRYSTAL_3.2X1.5
Q2: 24 MHz; CRYSTAL_5X3.2MM
R1, R2, R5, R6: .11; R0402
R3: DNP 1M, 1%; R0402
R4: 1M, 1%; R0402
R7, R13, R15, R16, R22, R23, R24, R25, R27, R30, R32, R54, R60: 10k, 1%; R0402
R8, R10, R17, R20, R21, R37, R38, R39, R40, R41: 0, 1%; R0402
R9: 27k, 1%; R0402
R11, R12, R52, R53: 1.5k, 1%; R0402
R14: 33; R0402
R18, R19, R55: 4.75k, 1%; R0402
R26, R28, R29, R31, R33, R34, R35, R42, R43, R44, R45, R46, R47, R48, R49, R50: 100k, 1%; R0402
R36: 22; R0402
R51: .1, R0805; R0805
R56: 499; R0402
R57, R66: DNP; R0402
R58: 10k 1%; R0402
R59: 40.2k 1%; R0402
R61, R62, R63, R64: 1k; R0402
R65: DNP 499; R0402
R67: DNP 10k 1%; R0402
R68: DNP 40.2k 1%; R0402
RESET1: MINI_PUSHBUTTON
T1: MMBT2907; SOT23-BEC
T2: DNP MMBT2907; SOT23-BEC
TP1, TP2, TP3, TP4, TP5, TP6, TP7, TP8: TESTPAD_W_HOLE_1X1
U1, U2: TMC2208-LA-T; QFN50P500X500X90-29N
USR1, USR2, USR3, USR4: LTST-C191TBKT; 0603-LED
X1: 10118241-001RLF; HDMI-TYPE-D-10118241
X2: USB_HOST_W_CHASSIS_GND; USB_HOST_HORIZONTAL_W_CHASSIS_GND
X3: SCHA5B0200
X4: PJ-102B; CUI_PJ-102B
X5: 10118192-0001LF; 10118192-0001LF(MICRO-USB-B-AMPHENOL-FCI)

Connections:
/12MHZ: FB4.2, IC3.27
/12M_LOOP: IC4.2, IC4.3
/AIN1: IC1.C7, J3.10
/BAT_TEMP: IC1.W1, TP8.P$1
/BAT_VOLT: IC1.Y1, TP7.P$1
/CEC: D1.C, IC3.30, X1.15
/CLKOUT2: FB3.1, R10.1
/DVI_5V: F1.1, R11.1, R12.1, X1.19
/EHRPWM2A: IC1.U10, U2.16
/EHRPWM2B: IC1.T10, U1.16
/EXT_SWING: IC3.34, R13.1
/GPIO0_7: R40.1, R41.1
/GPIO0_26: IC1.T11, U1.9
/GPIO0_27: IC1.U12, U2.10
/GPIO1_14: IC1.V13, U1.10
/GPIO1_15: IC1.U13, U2.9
/GPIO3_21: IC1.A14, R14.2
/HDMICLK_DIS#: IC1.V17, OSC1.1
/HDMI_INT: IC1.U16, IC3.50, R7.2
/HPD: IC3.31, X1.1
/I2C0_SCL: IC1.C16, IC1.C20, IC3.52, IC9.1, R52.2
/I2C0_SDA: IC1.C17, IC1.C19, IC3.51, IC9.3, R53.2
/LCD.CLOCK: IC3.4, R36.1
/LCD.D0.B0--B3: C29.1, IC1.R1, IC3.15, R50.2
/LCD.D1.B1--B4: C26.1, IC1.R2, IC3.13, R49.2
/LCD.D2.B2--B5: C23.1, IC1.R3, IC3.12, R47.2
/LCD.D3.B3--B6: C20.1, IC1.R4, IC3.11, R48.1
/LCD.D4.B4--B7: C18.1, IC1.T1, IC3.10, R46.1
/LCD.D5.G0--G2: C16.1, IC1.T2, IC3.7, R45.1
/LCD.D6.G1--G3: C14.1, IC1.T3, IC3.6, R44.2
/LCD.D7.G2--G4: C13.1, IC1.T4, IC3.3, R43.2
/LCD.D8.G3--G5: C12.1, IC1.U1, IC3.2, R42.2
/LCD.D9.G4--G6: C11.1, IC1.U2, IC3.1, R35.2
/LCD.D10.G5--G7: C10.1, IC1.U3, IC3.64, R34.2
/LCD.D11.R0--R3: C9.1, IC1.U4, IC3.60, R33.2
/LCD.D12.R1--R4: C8.1, IC1.V2, IC3.59, R31.2
/LCD.D13.R2--R5: C7.1, IC1.V3, IC3.58, R29.2
/LCD.D14.R3--R6: C6.1, IC1.V4, IC3.57, R28.1
/LCD.D15.R4--R7: C5.1, IC1.T5, IC3.56, R26.2
/LCD.ENABLE: IC3.20, R39.1
/LCD.HSYNC: IC3.22, R38.1
/LCD.VSYNC: IC3.21, R37.1
/LDO_PGOOD: IC1.B5, IC1.B20
/M1A+: J3.1, U2.24
/M1A-: J3.2, U2.21
/M1B+: J3.3, U2.26
/M1B-: J3.4, U2.1
/M2A+: J3.5, U1.24
/M2A-: J3.6, U1.21
/M2B+: J3.7, U1.26
/M2B-: J3.8, U1.1
/MCU.LCD.CLK: IC1.V5, R36.2
/MCU.LCD.EN: IC1.R6, R39.2
/MCU.LCD.HS: IC1.R5, R38.2
/MCU.LCD.VS: IC1.U5, R37.2
/PMIC_INT: IC1.B18, IC1.B19
/PMIC_NWAKEUP: IC1.A19, IC1.C5
/PMIC_PGOOD: IC1.A20, IC1.B15, IC2.2
/SD.CD: IC1.C15, R32.1, X3.CD
/SD.CLK: IC1.G17, R24.1, X3.5
/SD.CMD: IC1.G18, R25.1, X3.3
/SD.D0: IC1.G16, R23.1, X3.7
/SD.D1: IC1.G15, R22.1, X3.8
/SD.D2: IC1.F18, R30.1, X3.1
/SD.D3: IC1.F17, R27.1, X3.2
/SPI1_CS0: IC1.C12, IC3.25
/SPI1_D0: IC1.B13, IC3.24
/SPI1_SCLK: IC1.A13, IC3.23
/SYS_RESET#: C42.1, IC1.A10, IC2.4, R15.2, RESET1.3, RESET1.4
/TEST: IC3.49, R8.2
/TIMER4: IC1.R7, U2.19
/TIMER6: IC1.U6, U1.19
/TX0+: IC3.40, IC6.5, X1.9
/TX0-: IC3.39, IC6.4, X1.11
/TX1+: IC3.43, IC5.2, X1.6
/TX1-: IC3.42, IC5.1, X1.8
/TX2+: IC3.45, IC5.5, X1.3
/TX2-: IC3.44, IC5.4, X1.5
/TXC+: IC3.38, IC6.2, X1.12
/TXC-: IC3.37, IC6.1, X1.14
/UART1_TXD: IC1.D15, P2.1
/UART2_RXD: IC1.A17, P1.1
/USB1_DRVVBUS: IC1.F15, IC7.4, R16.1
/USB1_OC#: IC1.T16, IC7.5, R20.2
/USB1_VBUS: FB5.2, IC1.T18
/USB.CLIENT.D+: IC1.N17, IC10.1, X5.D+
/USB.CLIENT.D-: IC1.N18, IC10.2, X5.D-
/USB.CLIENT.ID: IC1.P16, IC10.3, X5.ID
/USB.HOST.D+: IC1.R17, IC8.1, X2.3
/USB.HOST.D-: IC1.R18, IC8.2, X2.2
/USR0: IC1.V15, R64.2
/USR1: IC1.U15, R63.2
/USR2: IC1.T15, R62.2
/USR3: IC1.V16, R61.2
/VIN_BAT: IC1.Y2, IC1.Y3, TP6.P$1
/XDMA_EVENT_INTRO: FB2.2, IC4.1
AGND: IC1.A6, IC1.A9, IC1.E8
CGND: MGT1.P$1, MGT2.P$1, MGT3.P$1, MGT4.P$1, R51.2, X1.CG1, X1.CG2, X1.CG3, X1.CG4, X2.5, X2.6, X3.CGND1, X3.CGND2, X3.CGND3, X3.CGND4, X3.CGND5, X3.CGND6, X5.CGND1, X5.CGND2, X5.CGND3, X5.CGND4, X5.CGND5, X5.CGND6
GND: C5.2, C6.2, C7.2, C8.2, C9.2, C10.2, C11.2, C12.2, C13.2, C14.2, C15.1, C16.2, C18.2, C20.2, C21.1, C22.2, C23.2, C24.1, C25.2, C26.2, C27.1, C28.2, C29.2, C30.2, C31.2, C32.2, C33.2, C34.2, C35.1, C38.2, C39.1, C40.1, C41.1, C42.2, C43.2, C44.-, C45.2, C46.2, C47.2, C48.2, C49.2, IC1.A1, IC1.A18, IC1.E19, IC1.E20, IC1.F8, IC1.F19, IC1.G8, IC1.G9, IC1.G11, IC1.G12, IC1.G19, IC1.H6, IC1.H7, IC1.H8, IC1.H9, IC1.H10, IC1.H12, IC1.H19, IC1.J6, IC1.J7, IC1.J8, IC1.J9, IC1.J10, IC1.J11, IC1.J19, IC1.J20, IC1.K7, IC1.K9, IC1.K10, IC1.K11, IC1.K19, IC1.L10, IC1.L11, IC1.L12, IC1.L13, IC1.L19, IC1.M6, IC1.M7, IC1.M8, IC1.M9, IC1.M10, IC1.M12, IC1.M14, IC1.M19, IC1.N7, IC1.N10, IC1.N11, IC1.N14, IC1.N19, IC1.N20, IC1.P19, IC1.P20, IC1.R19, IC1.R20, IC1.T19, IC1.T20, IC1.U19, IC1.V1, IC1.V18, IC1.V19, IC1.W2, IC1.W3, IC1.W5, IC1.W6, IC1.W7, IC1.W8, IC1.W9, IC1.W10, IC1.W11, IC1.W12, IC1.W13, IC1.W14, IC1.W15, IC1.W16, IC1.W17, IC1.W18, IC1.W19, IC1.W20, IC1.Y7, IC1.Y10, IC1.Y12, IC1.Y15, IC1.Y18, IC2.3, IC3.8, IC3.9, IC3.16, IC3.17, IC3.18, IC3.19, IC3.53, IC3.54, IC3.61, IC3.62, IC3.63, IC3.65, IC4.4, IC5.3, IC5.8, IC6.3, IC6.8, IC7.1, IC7.9, IC8.4, IC9.2, IC10.4, OSC1.2, P1.2, P2.2, R1.2, R2.2, R5.2, R6.2, R8.1, R13.2, R16.2, R17.2, R19.2, R26.1, R29.1, R31.1, R33.1, R34.1, R35.1, R42.1, R43.1, R44.1, R47.1, R49.1, R50.1, R51.1, R55.1, R60.1, RESET1.1, RESET1.2, U1.2, U1.3, U1.18, U2.2, U2.3, U2.18, USR1.K, USR2.K, USR3.K, USR4.K, X1.4, X1.7, X1.10, X1.13, X1.16, X2.4, X3.6, X3.GND, X4.2, X5.GND
HDMI_1V8: C22.1, C25.1, C28.1, C30.1, C31.1, C32.1, C33.1, C34.1, FB1.2, IC3.5, IC3.14, IC3.29, IC3.35, IC3.36, IC3.41, IC3.46, IC3.47, IC3.48, IC3.55
unnamed: C1.1, IC1.M20, Q2.2, R4.2
unnamed: C1.2, C2.2, IC1.L20
unnamed: C2.1, IC1.K20, Q2.1, R4.1
unnamed: C3.1, IC1.H20, Q1.P$1, R3.2
unnamed: C3.2, C4.2, IC1.G20
unnamed: C4.1, IC1.F20, Q1.P$2, R3.1
unnamed: C15.2, U1.8
unnamed: C17.2, U1.6
unnamed: C19.1, U1.4
unnamed: C19.2, U1.5
unnamed: C35.2, U2.8
unnamed: C36.2, U2.6
unnamed: C37.1, U2.4
unnamed: C37.2, U2.5
unnamed: C45.1, FB5.1, FB6.1, IC7.6, IC7.7, IC7.8, IC8.6
unnamed: D1.A, R9.2
unnamed: FB2.1, IC1.A15
unnamed: FB3.2, IC1.D14
unnamed: FB4.1, IC4.5
unnamed: FB6.2, X2.1
unnamed: IC1.B4, R60.2
unnamed: IC1.B12, R40.2
unnamed: IC1.C6, IC1.D19
unnamed: IC1.C9, R18.2, R19.1
unnamed: IC1.C18, R41.2
unnamed: IC1.D13, R10.2
unnamed: IC1.P15, R21.1
unnamed: IC1.P17, R17.1
unnamed: IC3.32, R12.2, X1.18
unnamed: IC3.33, R11.2, X1.17
unnamed: IC9.5, R54.2, TP5.P$1
unnamed: IC11.1, R57.2, R58.2, R59.1
unnamed: IC11.2, R56.2, R57.1, T1.B
unnamed: IC12.1, R66.2, R67.2, R68.1
unnamed: IC12.2, R65.2, R66.1, T2.B
unnamed: OSC1.3, R14.1
unnamed: PWR1.K, R55.2
unnamed: R1.1, U1.23
unnamed: R2.1, U1.27
unnamed: R5.1, U2.23
unnamed: R6.1, U2.27
unnamed: R61.1, USR1.A
unnamed: R62.1, USR2.A
unnamed: R63.1, USR3.A
unnamed: R64.1, USR4.A
unnamed: TP1.P$1, U1.11
unnamed: TP2.P$1, U1.12
unnamed: TP3.P$1, U2.11
unnamed: TP4.P$1, U2.12
unnamed: U1.7, U1.20, U1.25
unnamed: U2.7, U2.20, U2.25
SYS_5V: C44.+, F1.2, IC1.W4, IC1.Y4, IC7.2, IC7.3
USB_DC: C49.1, IC1.Y8, IC1.Y9, IC10.6, R21.2, X5.VBUS
VDD_1V8: FB1.1, IC1.D10, IC1.E9, IC1.N16, IC1.R16, IC2.5, IC11.3, IC12.3, R59.2, R68.2, T1.C, T2.C
VDD_3V3A: IC1.N5, IC1.P5, IC1.P6, IC1.P7, R56.1, R58.1, T1.E
VDD_3V3AUX: IC1.Y11, PWR1.A
VDD_3V3B: C38.1, C43.1, C46.1, C47.1, C48.1, IC1.U20, IC1.V20, IC4.6, IC4.7, IC4.8, IC9.4, OSC1.4, R7.1, R9.1, R15.1, R18.1, R20.1, R22.2, R23.2, R24.2, R25.2, R27.2, R28.2, R30.2, R32.2, R45.2, R46.2, R48.2, R52.1, R53.1, R54.1, R65.1, R67.1, T2.E, X3.4
VDD_5V: C17.1, C21.2, C24.2, C27.2, C36.1, C39.2, C40.2, C41.2, IC1.Y5, IC1.Y6, U1.22, U1.28, U2.22, U2.28, X4.1
VDD_ADC: IC1.A4, IC1.A5, IC1.B9, IC1.D8

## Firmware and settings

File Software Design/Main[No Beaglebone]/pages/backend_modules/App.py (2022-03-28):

from Eventhandler import Eventhandler
import time
from Database import *


if __name__ == '__main__':
    event_handler = Eventhandler()
    #setSetting("TargetW", 1)
    event_handler.playHaptic()
    time.sleep(1)
    event_handler.playSound()
    
    
    #event_handler.calibrate()
    
    #print(str(getSetting("FSpeed")))
    #print(str(getSetting("MSpeed")))
    #print(str(getSetting("SSpeed")))
    #while(1):
        #time.sleep(1)
        #print(getSetting("CurrentW"))

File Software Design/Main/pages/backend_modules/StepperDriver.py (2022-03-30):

import Adafruit_BBIO.PWM as PWM
import Adafruit_BBIO.GPIO as GPIO
from pages.backend_modules.Database import *
import time


#Angle Motor Driver Board 
AStep = "P8_19"
ADir = "P8_7"
ASlp = "P8_9"
AMS1 = "P8_15"
AMS2 = "P8_17"
AEna = "P8_8"
#Trickler Motor Driver Board
MStep = "P8_13"
MDir = "P8_10"
MSlp = "P8_12"
MMS1 = "P8_14"
MMS2 = "P8_16"
MEna = "P8_26"



#Angle Driver Motor Board
GPIO.setup(AStep, GPIO.OUT, GPIO.PUD_DOWN)
GPIO.setup(ADir, GPIO.OUT, GPIO.PUD_DOWN)
GPIO.setup(ASlp, GPIO.OUT, GPIO.PUD_DOWN)
GPIO.setup(AMS1, GPIO.OUT, GPIO.PUD_UP)
GPIO.setup(AMS2, GPIO.OUT, GPIO.PUD_UP)
GPIO.setup(AEna, GPIO.OUT, GPIO.PUD_UP)

#Trickler Driver Motor Board
#GPIO.setup(MStep, GPIO.OUT)#, GPIO.PUD_DOWN)
GPIO.setup(MDir, GPIO.OUT, GPIO.PUD_DOWN)
GPIO.setup(MSlp, GPIO.OUT, GPIO.PUD_DOWN)
GPIO.setup(MMS1, GPIO.OUT, GPIO.PUD_UP)
GPIO.setup(MMS2, GPIO.OUT, GPIO.PUD_UP)
GPIO.setup(MEna, GPIO.OUT, GPIO.PUD_UP)

def Start(speed):
    GPIO.output(MEna,GPIO.LOW)
    GPIO.output(MSlp, GPIO.HIGH) #Turns on Driver Board
    GPIO.output(MDir, GPIO.LOW) # Sets Direction
    GPIO.output(MMS1, GPIO.LOW) # Sets MicroStep Switch 1
    GPIO.output(MMS2, GPIO.HIGH) # Sets MicroStep Switch 2
    
    if speed == 1:
        PWM.start(MStep, 50, 1000)
    elif speed == 2:
        PWM.start(MStep, 50, 1500)
    else:
        PWM.start(MStep, 50, 2000)
        
def Stop():
    PWM.stop(MStep)
    PWM.cleanup()
    GPIO.output(MEna, GPIO.HIGH)
    GPIO.output(MSlp, GPIO.LOW)
 
    
def cal():
    speeds = ["FSpeed", "MSpeed", "SSpeed"]
    for i in range(3):
        start = float(getSetting("CurrentW"))
        Start(i)
        time.sleep(2)
        Stop()
        time.sleep(5)
        finish = float(getSetting("CurrentW"))
        setSetting(speeds[i-1], str((finish-start)/2))
        
def autorun():
    slow = float(getSetting("SSpeed"))
    med = float(getSetting("MSpeed"))
    fast = float(getSetting("FSpeed"))
    target = float(getSetting("TargetW"))
    
    gab = target - float(getSetting("CurrentW"))
    while(gab > .1):
        if(gab > fast/2):
            Start(3)
        elif(gab > med/2):
            Start(2)
        elif(gab > slow/2):
            Start(1)
        else:
            print("finish")
            break
        time.sleep(.5)
        Stop()
        time.sleep(4)
        gab = target - float(getSetting("CurrentW"))
        
        
def angleChange(direction):
    
    GPIO.output(AEna,GPIO.LOW)
    GPIO.output(ASlp, GPIO.HIGH) #Turns on Driver Board
    if direction:
        GPIO.output(ADir) # Sets Direction
    else:
        GPIO.output(ADir, GPIO.HIGH)
    GPIO.output(AMS1, GPIO.LOW) # Sets MicroStep Switch 1
    GPIO.output(AMS1, GPIO.HIGH) # Sets MicroStep Switch 2
    PWM.start(AStep, 50, 1000)

    PWM.stop(AStep)
    PWM.cleanup()
    GPIO.output(AEna, GPIO.HIGH)
    GPIO.output(ASlp, GPIO.LOW)

    
    
        

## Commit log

2022-01-16 basic threading framework
2022-01-19 fixed event handler and threading
    [Eventhandler.py]
2022-01-19 added framework for driver classes
2022-02-09 tried out some other ways of using tkinter
    [GUI Block Diagram.xlsx]
2022-02-14 backend framework
2022-02-14 Update StepperDrivers.py
    added empty functions to run GUI test
2022-02-16 got page switching to work :D
2022-03-16 calibrate dialogue
2022-03-30 found a guide to fix feed buttons
2022-03-30 stop buttons
2022-03-31 Added Close on Unit Popup and other things
    [GUI Block Diagram.xlsx]
2022-04-01 Arrow Buttons on Load and View
2022-04-01 added database with save button
2022-04-01 fixed card insert function
    [Database.py]
2022-04-04 added BOM
    [BillOfMaterials_Template.xlsx]
2022-04-04 added budget
    [BillOfMaterials.xlsx, Budget.xlsx]
2022-04-04 file moving
    [GUI Block Diagram.xlsx]

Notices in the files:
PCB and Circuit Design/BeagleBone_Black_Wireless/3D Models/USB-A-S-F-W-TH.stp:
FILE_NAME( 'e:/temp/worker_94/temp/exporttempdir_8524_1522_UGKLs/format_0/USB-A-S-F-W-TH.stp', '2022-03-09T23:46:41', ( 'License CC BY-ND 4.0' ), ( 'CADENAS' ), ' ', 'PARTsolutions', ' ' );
